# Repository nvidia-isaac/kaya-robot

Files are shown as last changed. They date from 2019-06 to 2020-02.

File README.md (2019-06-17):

# kaya-robot

Kaya is an open-source robot powered by NVIDIA's Isaac SDK and the Jetson Nano. 

This repository contains 3D-printable and editable CAD files in the `cad-files` folder (STL, STEP, IGES), as well as a complete bill of materials and assembly instructions for [NVIDIA Kaya](doc/assemble_kaya.md) in the `doc` folder.

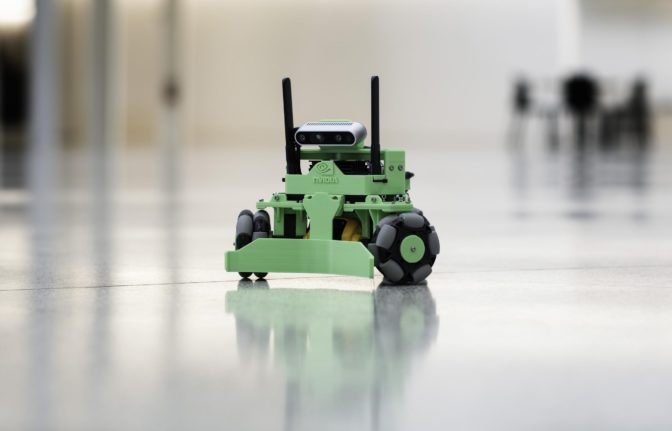
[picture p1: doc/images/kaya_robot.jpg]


Kaya is intended to provide an accessible starting point for robotics development, and a number of sample apps for Kaya come packaged with the Isaac SDK.

For more information on Kaya and the Isaac SDK, see the [NVIDIA Isaac SDK Documentation](https://docs.nvidia.com/isaac/isaac/doc/index.html).

You can also join NVIDIA's developer community to ask questions and share your projects on the [Isaac SDK Forums](https://devtalk.nvidia.com/default/board/375/sdk/)!

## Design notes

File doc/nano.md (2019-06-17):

How to Get Started With Jetson Nano
===================================

This section describes how to flash, install wireless connectivity, and
run Isaac SDK sample applications on the Jetson Nano device. To get
started with Nano in general, from the very beginning, see [Getting
Started with Jetson Nano Developer
Kit](https://developer.nvidia.com/embedded/learn/get-started-jetson-nano-devkit).

How to Flash Jetson Nano
------------------------

Nano can be flashed in two ways:

-   Via an SD Card: See the procedures in [Getting Started with Jetson
    Nano Developer
    Kit](https://developer.nvidia.com/embedded/learn/get-started-jetson-nano-devkit).
-   Via SDK Manager: See the procedures in [SDK Manager User
    Guide](https://docs.nvidia.com/sdk-manager)

Use those documents to determine the best method for your use case.

Connecting a Wi-Fi/Bluetooth Card
---------------------------------

The Intel 8265 is used for Wi-Fi and Bluetooth connectivity. Use the
following steps to install a Wi-Fi/Bluetooth card for Jetson Nano.

1.  To access the M.2 slot on the carrier board, remove the two screws
    on the side and open the SODIMM latches using both your hands.

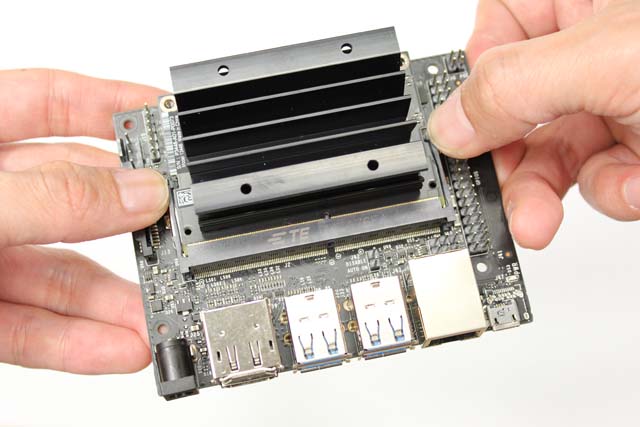
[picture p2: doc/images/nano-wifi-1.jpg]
    

2.  When the Jetson Nano module pops up, slide it out gently.

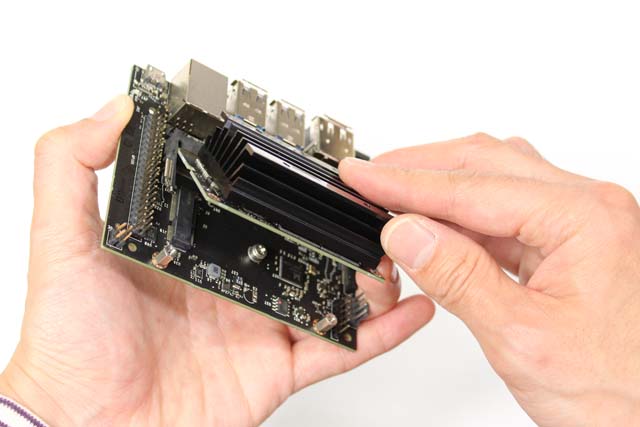
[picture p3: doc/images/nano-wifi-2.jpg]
    

3.  Take out the Intel wireless card, attach antenna on its U.FL sockets
    before inserting the card to the M.2 socket. Attaching the antena on
    the sockets requires a patience and getting used to. Use your nail
    to gently apply a force. You don't need that much force to clamp
    that in once you are in the right position.

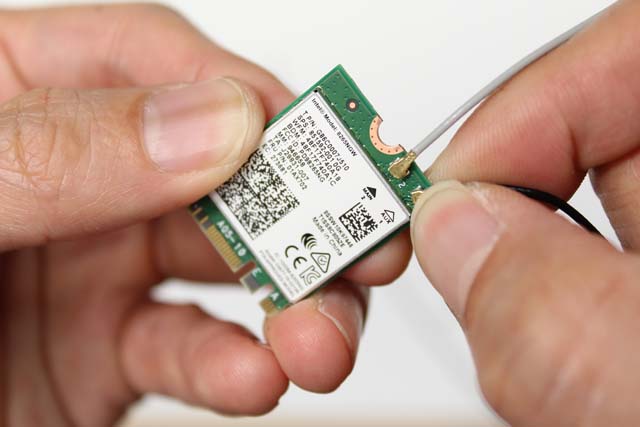
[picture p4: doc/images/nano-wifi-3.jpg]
    

4.  Slide the Intel 8265 card into the socket.

    

5.  Fix the Intel 8265 card in place with a screw, and replace the
    Jeston Nano module. Make sure to use the correct screws in each
    case.

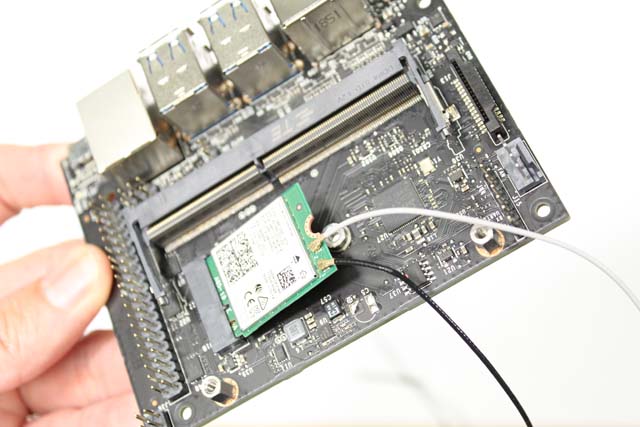
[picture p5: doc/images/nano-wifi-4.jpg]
    

Getting the IP Address
----------------------

Obtain the IP address of Jetson Nano with the following steps:

1.  If necessary, connect a keyboard, mouse, and display, and boot the
    device as shown in the [Setup and First
    Boot](https://developer.nvidia.com/embedded/learn/get-started-jetson-nano-devkit#setup)
    section of Getting Started with Jetson Nano Developer Kit.
2.  At a terminal prompt, enter the following command:

        bob@jetson:~/$ ip addr show

Sample Applications to Run on Jetson Nano
-----------------------------------------

This section describes the steps to run two sample applications on
Jetson Nano. The first does not require any peripherals. The second one
is a more useful application that requires a camera to be connected.

Other applications can be also deployed and run using the methods
described here.

### Ping

1.  On the host system where the Isaac SDK is installed, start by typing
    the following on your host machine with Isaac SDK.

>     bob@desktop:~/isaac$ /engine/build/deploy.sh -d jetpack42 -h <nano_ip> -p //apps/tutorials/ping:ping-pkg
>
> You might need to use the --remote\_user USER flag if the user name on
> the robot is not nvidia.

1.  Change to the directory on your Jetson Nano and run the application
    with the following commands:

>     bob@jetson:~/$ cd deploy/bob/ping-pkg/
>     bob@jetson:~/deploy/bob/ping-pkg$ ./apps/tutorials/ping/ping

Where "bob" is your username on the host system. You should see "Hello
World!" being printed every 1.5 seconds.

### OpenCV Edge Detection

1.  For this sample, connect a camera to one of the USB ports on the
    Jetson Nano.
2.  On the host system where the Isaac SDK is installed, type the
    following command:

>     bob@jetson:~/isaac$ ./engine/build/deploy.sh -d jetpack42 -h <nano_ip> -p //apps/tutorials/opencv_edge_detection:opencv_edge_detection-pkg
>
> You might need to use the --remote\_user USER flag if the user name on
> the robot is not nvidia.

1.  Change to the directory on your Jetson Nano and run the application
    with the following commands:

>     bob@jetson:~/$ cd deploy/bob/opencv_edge_detection-pkg/
>     bob@jetson:~/deploy/bob/opencv_edge_detection-pkg/$ ./apps/tutorials/opencv_edge_detection/opencv_edge_detection

1.  To view the results, load http://&lt;nano\_ip&gt;:3000/ in your
    browser. Make sure that the application is running when you are
    loading the webpage.

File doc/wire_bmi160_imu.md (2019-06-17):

Wire the BMI160 IMU to the Jetson Nano or Xavier
================================================

The Bosch Sensortec BMI160 Inertial Measurement Unit attaches to the
Jetson board via the 40 pin GPIO Expansion Header. The IMU sample app is
configured to look for the BMI160 on I2C bus 1. Here are instructions on
how to wire the IMU to I2C bus 1.

Jetson Nano
-----------

From the BMI160 to the Jetson Nano 40 pin connector attach VIN to GPIO
1, GND to GPIO 6, SCL to GPIO 5, and SDA to GPIO 3.

<table style="width:25%;">
<colgroup>
<col width="12%" />
<col width="12%" />
</colgroup>
<thead>
<tr class="header">
<th>BMI160</th>
<th>GPIO</th>
</tr>
</thead>
<tbody>
<tr class="odd">
<td>VIN</td>
<td><blockquote>
<p>1</p>
</blockquote></td>
</tr>
<tr class="even">
<td>GND</td>
<td><blockquote>
<p>6</p>
</blockquote></td>
</tr>
<tr class="odd">
<td>SCL</td>
<td><blockquote>
<p>5</p>
</blockquote></td>
</tr>
<tr class="even">
<td>SDA</td>
<td><blockquote>
<p>3</p>
</blockquote></td>
</tr>
</tbody>
</table>

It is a little hard to see the wiring in these photos since the Nano is
attached to a robot, so multiple photos are included.

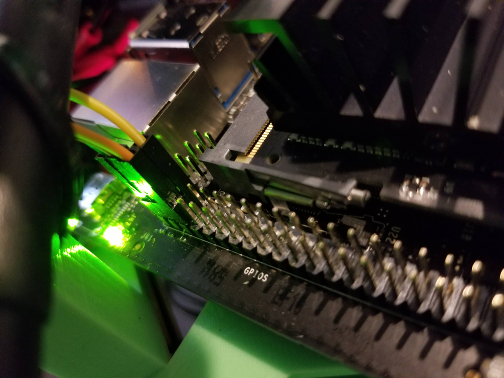
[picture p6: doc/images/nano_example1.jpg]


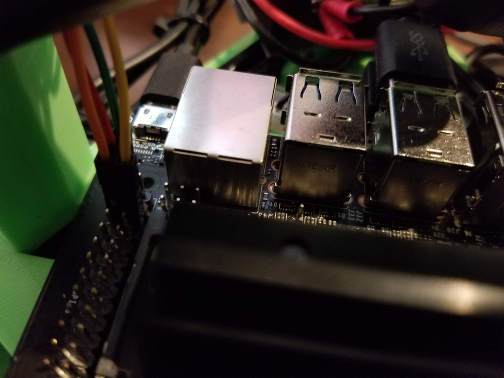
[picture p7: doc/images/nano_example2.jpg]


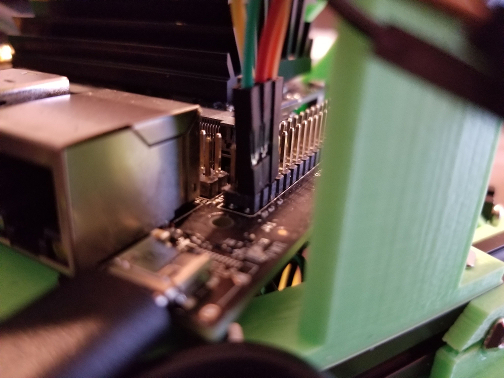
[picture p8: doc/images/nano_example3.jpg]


Wiring:

    Green wire:  VIN => GPIO 1
    Red wire:    SDA => GPIO 3
    Orange wire: SCL => GPIO 5
    Yellow wire: GND => GPIO 6

Jetson Xavier
-------------

From the BMI160 to the Jetson Xavier 40 pin connector attach VIN to GPIO
17, GND to GPIO 25, SCL to GPIO 28, and SDA to GPIO 27.

<table style="width:25%;">
<colgroup>
<col width="12%" />
<col width="12%" />
</colgroup>
<thead>
<tr class="header">
<th>BMI160</th>
<th>GPIO</th>
</tr>
</thead>
<tbody>
<tr class="odd">
<td>VIN</td>
<td><blockquote>
<p>17</p>
</blockquote></td>
</tr>
<tr class="even">
<td>GND</td>
<td><blockquote>
<p>25</p>
</blockquote></td>
</tr>
<tr class="odd">
<td>SCL</td>
<td><blockquote>
<p>28</p>
</blockquote></td>
</tr>
<tr class="even">
<td>SDA</td>
<td><blockquote>
<p>27</p>
</blockquote></td>
</tr>
</tbody>
</table>

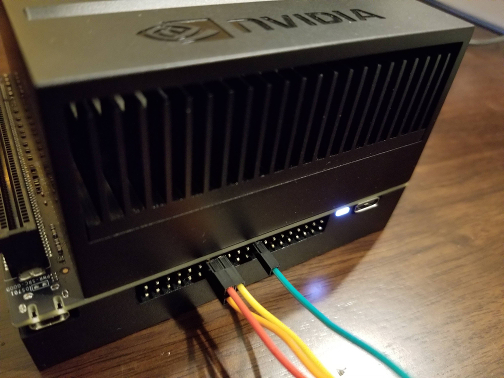
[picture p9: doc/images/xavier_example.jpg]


Wiring:

    Green wire:  VIN => GPIO 17
    Yellow wire: GND => GPIO 25
    Red wire:    SDA => GPIO 27
    Orange wire: SCL => GPIO 28

User Permissions
----------------

On the Jetson, `/dev/i2c-*` is owned by the user `root`, and are in the
group `i2c`. The sample app will need to run as either root, or by a
user in the i2c group.

To add the current user to the i2c group, use the following command:

    sudo usermod -a -G i2c $USER

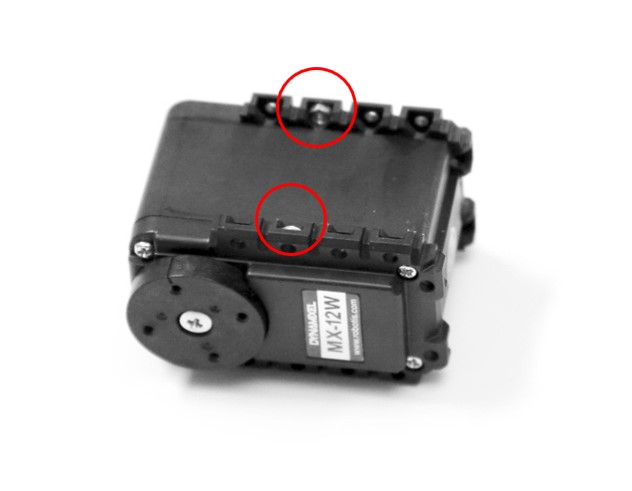
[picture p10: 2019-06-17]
doc/images/kaya2.jpg

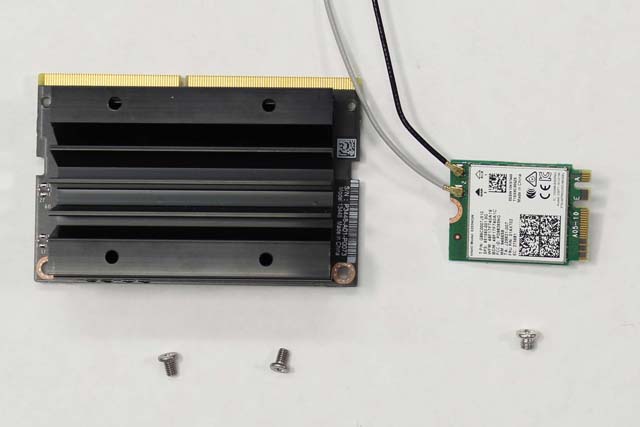
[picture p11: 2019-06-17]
doc/images/nano-wifi-5.jpg

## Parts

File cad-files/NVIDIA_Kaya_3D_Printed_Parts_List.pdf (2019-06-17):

# NVIDIA Kaya 3D Printed Parts List

All parts are shown in their intended print orientation (ie. print bed downward). Kaya_Nano_Base ● 0.15mm layer height suggested ● No support

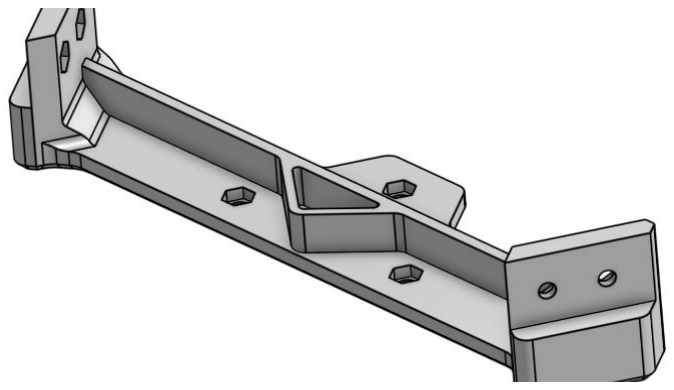
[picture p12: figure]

Kaya_Realsense_Bridge ● 0.15mm layer height suggested ● No support

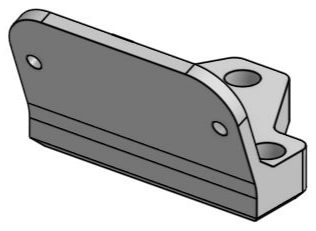
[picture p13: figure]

Kaya_Realsense_Mount ● 0.15mm layer height suggested ● No support

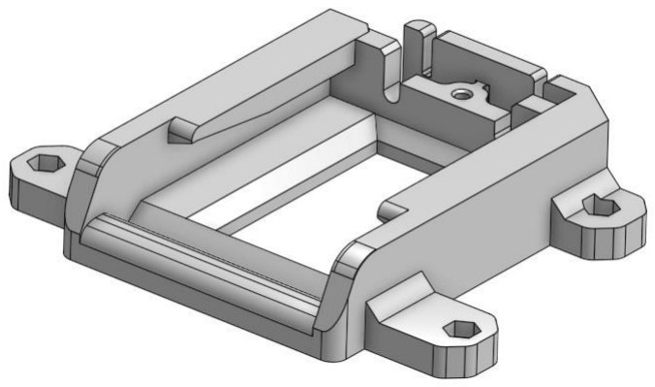
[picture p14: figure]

Kaya_Battery_Holder ● 0.15mm layer height suggested ● Support for internal undercut rails

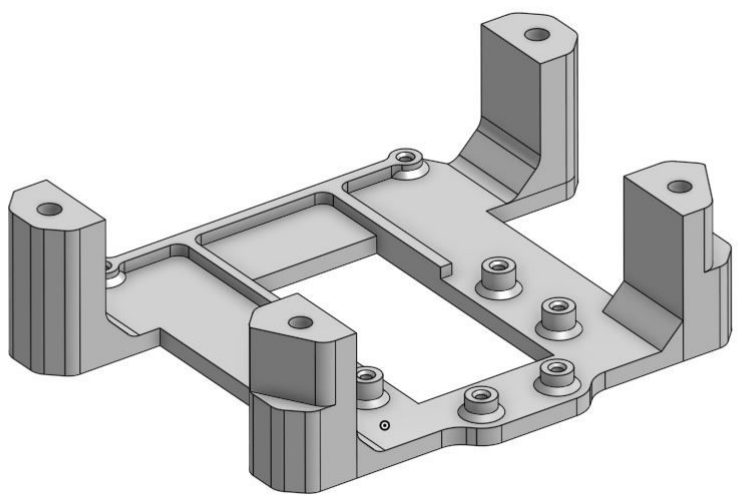
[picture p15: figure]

Kaya_Electronics_Bay ● 0.15mm layer height suggested ● No support

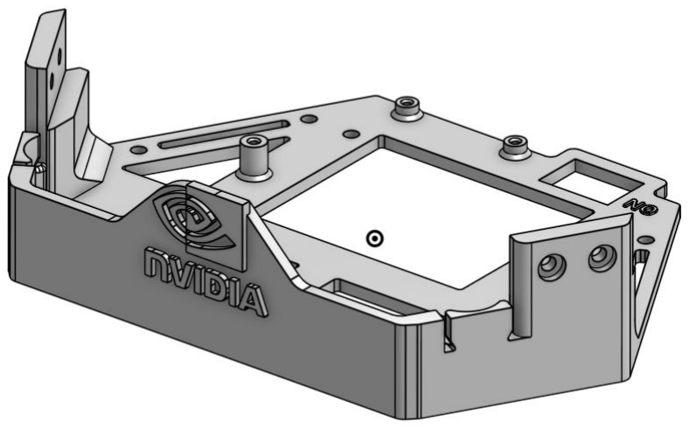
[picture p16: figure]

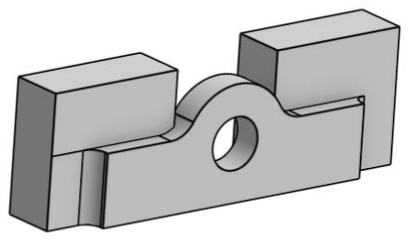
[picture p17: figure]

Kaya_Battery_Terminal_Holder ● 0.15mm layer height suggested ● No support

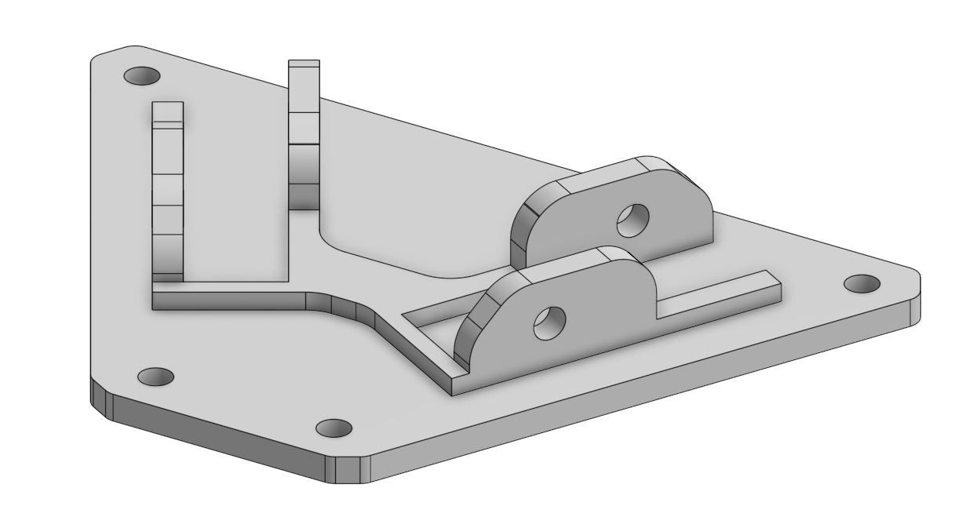
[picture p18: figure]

Kaya_Motor_Top_Plate ● 0.15mm layer height suggested ● No support *3x parts per unit

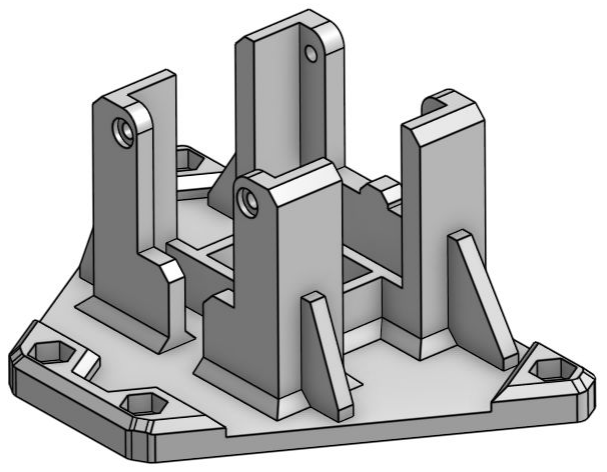
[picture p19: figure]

Kaya_Motor_Bottom_Plate ● 0.15mm layer height suggested ● No support *3x parts per unit


Kaya_Wheel_Hub_Outside ● 0.15mm layer height suggested ● No support *3x parts per unit

Kaya_Wheel_Hub_Inside ● 0.15mm layer height suggested ● No support *3x parts per unit


Kaya_Pusher_Mount ● 0.15mm layer height suggested ● No support


Kaya_Pusher ● 0.15mm layer height suggested ● Support for rear


Kaya_Terminal_Block_Cover ● 0.15mm layer height suggested ● Support for overhang mount hole

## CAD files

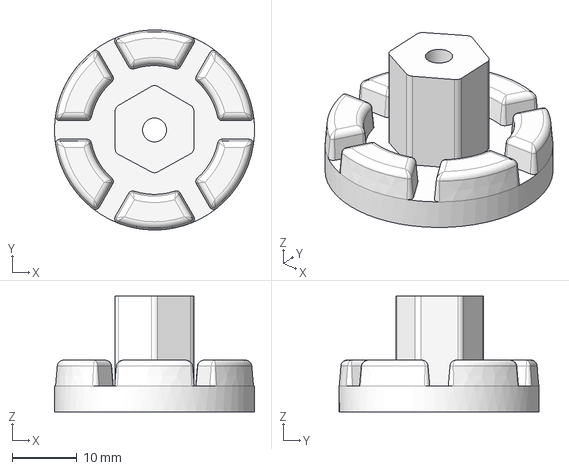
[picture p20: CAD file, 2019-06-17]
cad-files/Kaya_Wheel_Hub_Outside.step
30.9 x 30.9 x 17.9 mm

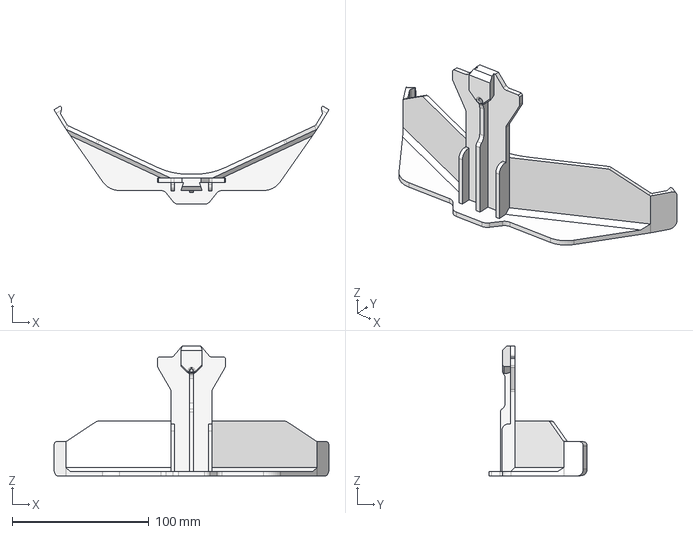
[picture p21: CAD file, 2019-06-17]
cad-files/Kaya_Pusher.step
201.5 x 72.0 x 95.0 mm

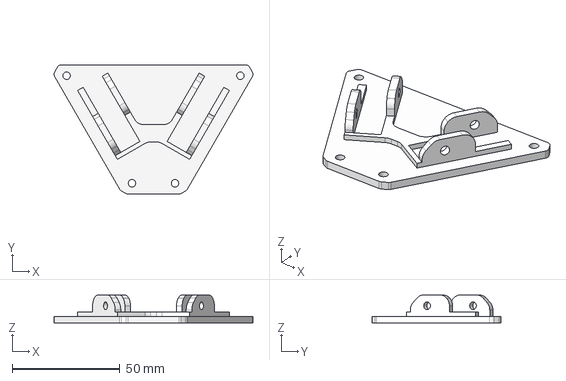
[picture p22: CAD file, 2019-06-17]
cad-files/Kaya_Motor_Top_Plate.step
92.5 x 60.0 x 13.0 mm

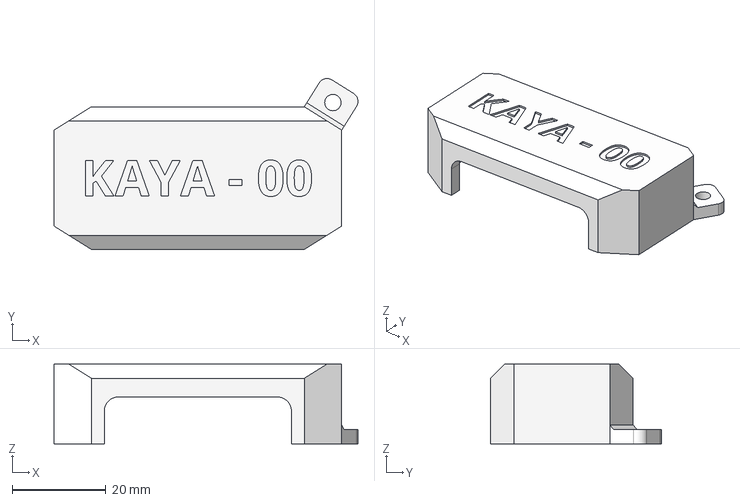
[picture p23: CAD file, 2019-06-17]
cad-files/Kaya_Terminal_Block_Cover.step
65.0 x 36.5 x 17.0 mm

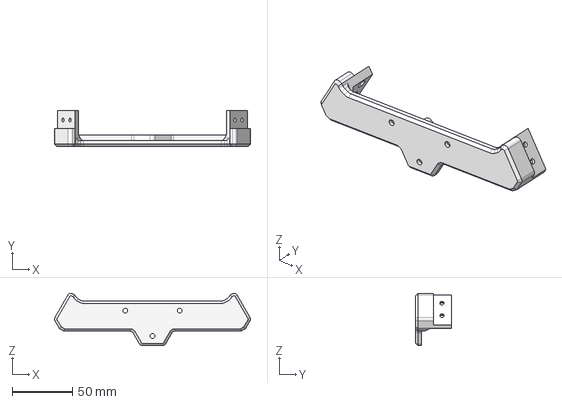
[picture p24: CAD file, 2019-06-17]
cad-files/Kaya_Realsense_Bridge.step
162.2 x 30.0 x 43.4 mm

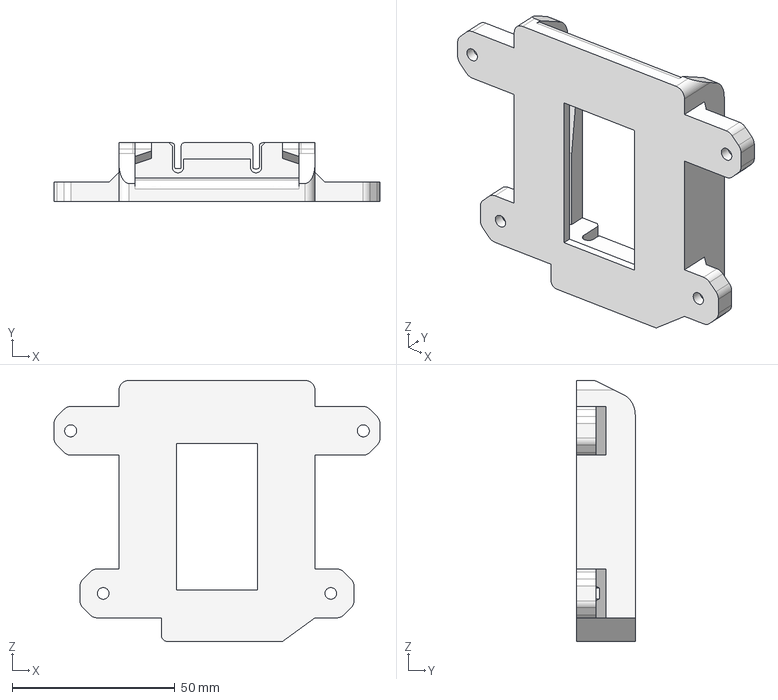
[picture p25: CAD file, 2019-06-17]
cad-files/Kaya_Battery_Holder.step
100.3 x 18.0 x 80.3 mm

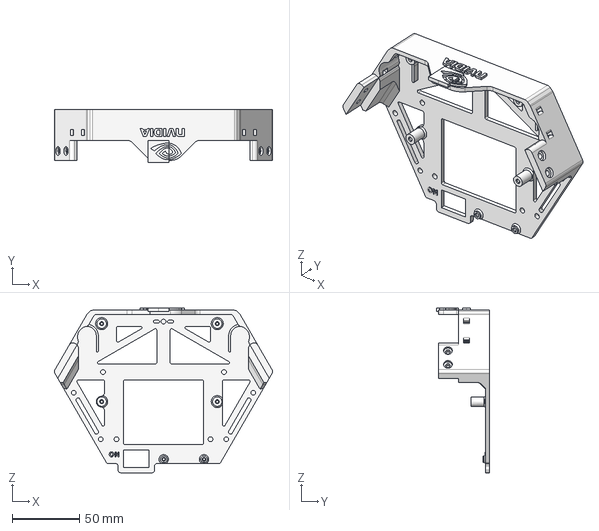
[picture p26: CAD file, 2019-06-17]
cad-files/Kaya_Nano_Base.step
162.2 x 39.6 x 122.4 mm

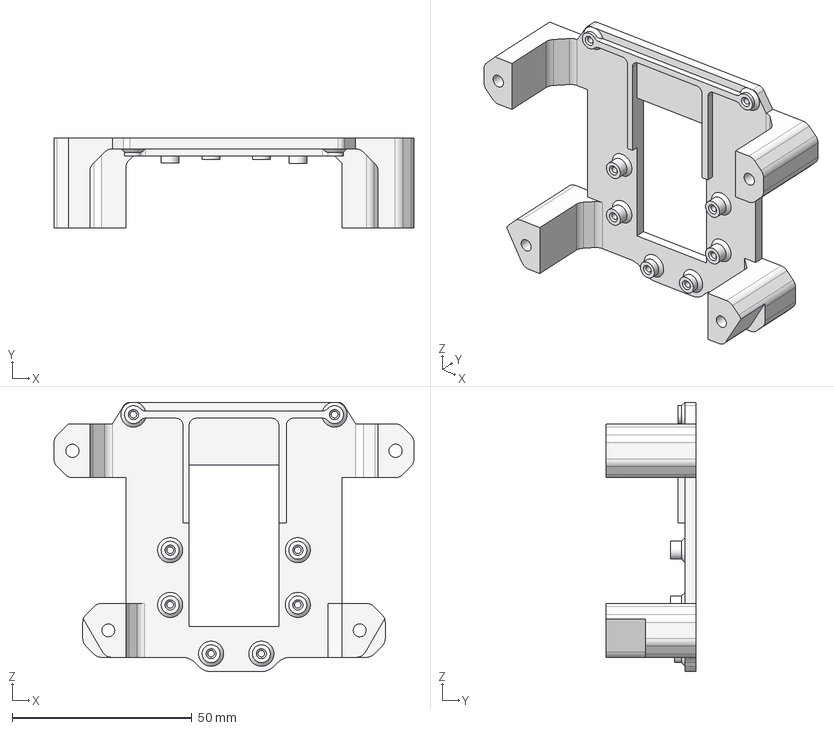
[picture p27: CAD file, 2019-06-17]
cad-files/Kaya_Electronics_Bay.step
100.3 x 25.0 x 75.0 mm

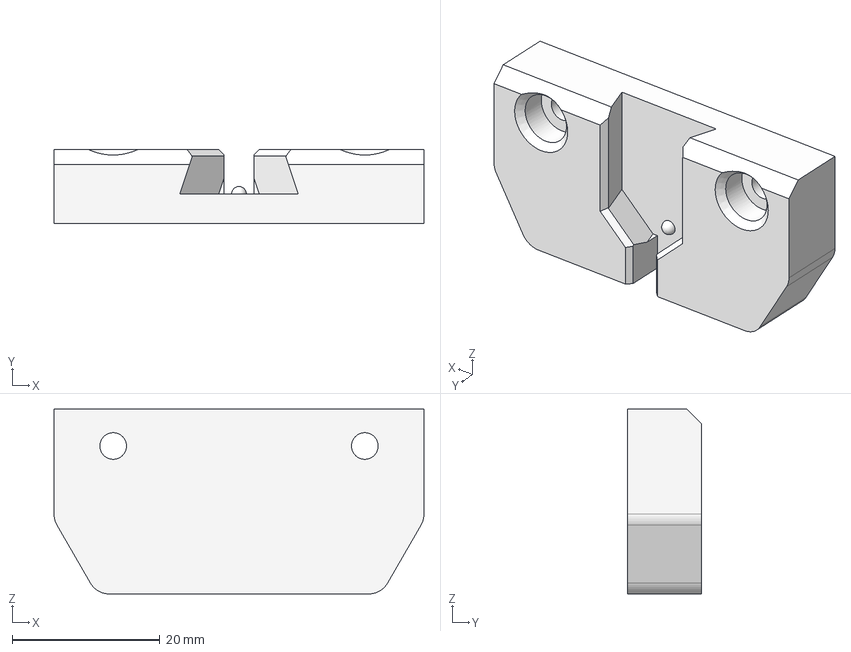
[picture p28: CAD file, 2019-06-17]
cad-files/Kaya_Pusher_Mount.step
50.0 x 10.0 x 25.0 mm

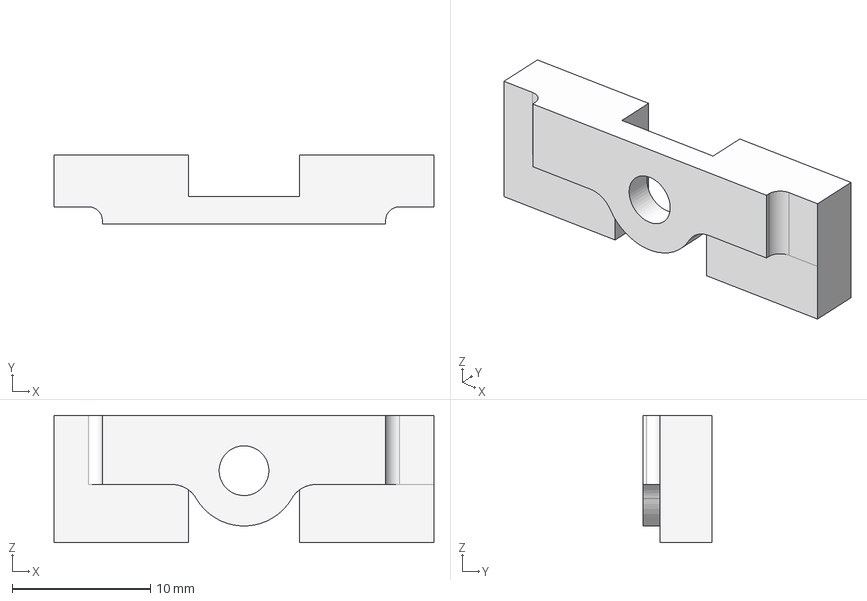
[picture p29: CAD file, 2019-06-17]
cad-files/Kaya_Battery_Terminal_Holder.step
27.5 x 5.00 x 9.20 mm

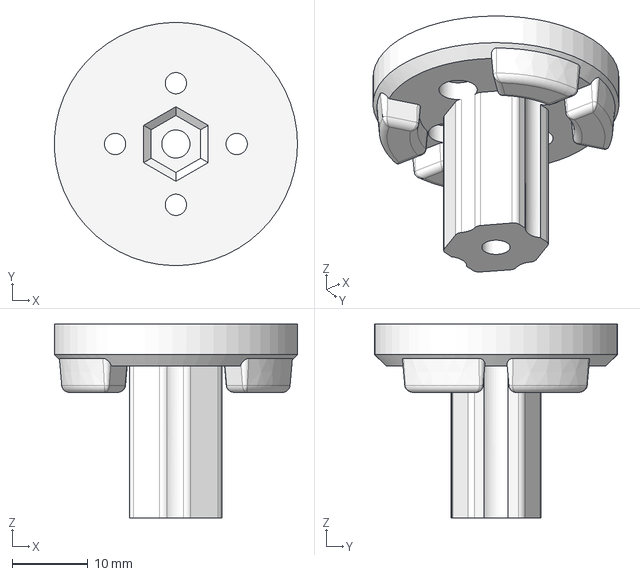
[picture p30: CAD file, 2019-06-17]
cad-files/Kaya_Wheel_Hub_Inside.step
32.0 x 32.0 x 25.5 mm

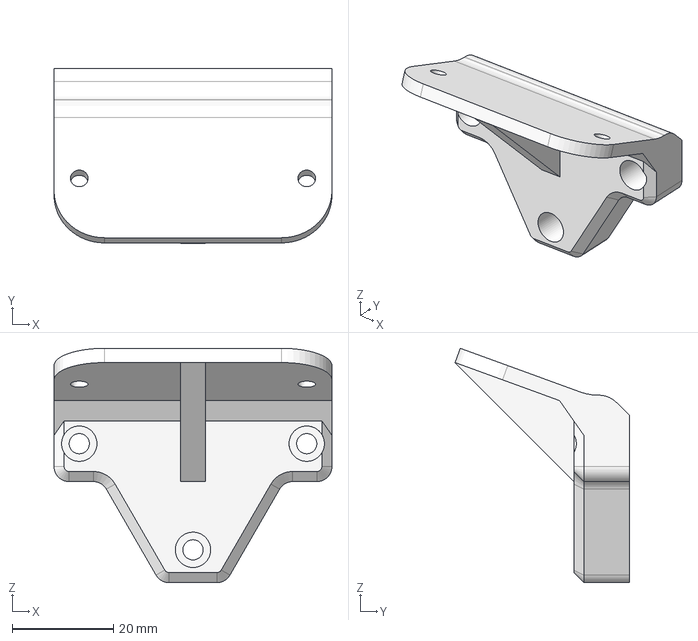
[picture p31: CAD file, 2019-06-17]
cad-files/Kaya_Realsense_Mount.step
55.0 x 34.6 x 46.4 mm

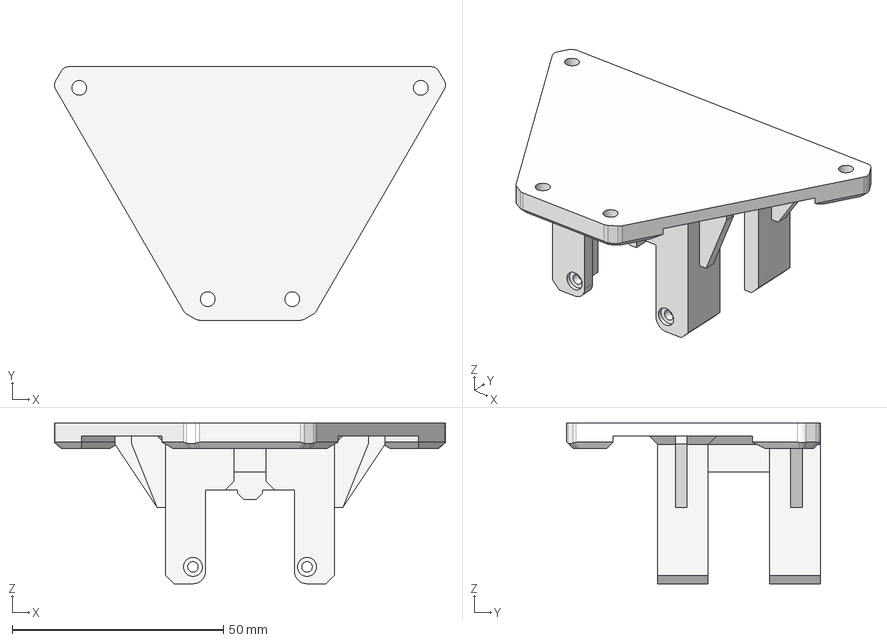
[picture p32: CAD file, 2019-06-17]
cad-files/Kaya_Motor_Bottom_Plate.step
92.5 x 60.0 x 38.0 mm

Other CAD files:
cad-files/Kaya_Battery_Holder.iges
cad-files/Kaya_Battery_Holder.stl
cad-files/Kaya_Battery_Terminal_Holder.iges
cad-files/Kaya_Battery_Terminal_Holder.stl
cad-files/Kaya_Electronics_Bay.iges
cad-files/Kaya_Electronics_Bay.stl
cad-files/Kaya_Motor_Bottom_Plate.iges
cad-files/Kaya_Motor_Bottom_Plate.stl
cad-files/Kaya_Motor_Top_Plate.iges
cad-files/Kaya_Motor_Top_Plate.stl
cad-files/Kaya_Nano_Base.iges
cad-files/Kaya_Nano_Base.stl
cad-files/Kaya_Pusher.iges
cad-files/Kaya_Pusher.stl
cad-files/Kaya_Pusher_Mount.iges
cad-files/Kaya_Pusher_Mount.stl
cad-files/Kaya_Realsense_Bridge.iges
cad-files/Kaya_Realsense_Bridge.stl
cad-files/Kaya_Realsense_Mount.iges
cad-files/Kaya_Realsense_Mount.stl
cad-files/Kaya_Terminal_Block_Cover.iges
cad-files/Kaya_Terminal_Block_Cover.stl
cad-files/Kaya_Wheel_Hub_Inside.iges
cad-files/Kaya_Wheel_Hub_Inside.stl
cad-files/Kaya_Wheel_Hub_Outside.iges

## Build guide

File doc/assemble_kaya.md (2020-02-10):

NVIDIA Kaya
===========

Kaya is a robot developed as a platform to demonstrate the power and
flexibility of the Isaac Robot Engine running on the NVIDIA Jetson Nano
platform. It has been intentionally designed using 3D printed parts and
hobbyist components to be as accessible as possible.



The Kaya Robot

Kaya features a three-wheeled holonomic drive which allows it to move in
any direction, regardless of where it is facing. A RealSense depth
camera allows Kaya to see the world around it in 3D, enabling features
like mapping, localization, and object recognition. An on-board IMU and
position feedback from the wheel motors provide accurate odometry
information. Power is provided via an easily-swapped and fast-charging
power tool battery. Outfitting the Jetson Nano with a Wi-Fi/Bluetooth
card allows you to interact with the robot using Isaac Sight over Wi-Fi,
and also allows you to connect a gamepad controller via Bluetooth.

Use the instructions in this section to build and operate your own Kaya
robot.

Parts
-----

For a list of 3D printed parts, and STL/STEP/IGES files for creating the parts,
see either the [`cad-files`](https://github.com/nvidia-isaac/kaya-robot/tree/master/cad-files) folder in this GitHub repository, or the [Isaac Developer
Downloads](https://developer.nvidia.com/isaac/downloads) website.

The following is a list of the off-the-shelf components needed for
building Kaya. Prices shown are approximate and subject to change by
vendors. Many of these components or suitable replacements are available
from a wide variety of sources, which you are encouraged to explore.

<table>
<thead>
<tr class="header">
<th><strong>PART NAME</strong></th>
<th><strong>VENDOR PART #</strong></th>
<th><strong>SOURCE</strong></th>
<th><strong>QTY</strong></th>
<th><strong>APPROX COST</strong></th>
</tr>
</thead>
<tbody>
<tr class="odd">
<td>3D Printed Parts</td>
<td>-</td>
<td><em>See 3D Printed Parts List</em></td>
<td>-</td>
<td>-</td>
</tr>
<tr class="even">
<td>NVIDIA Jetson Nano Developer Kit</td>
<td>945-13450-0000-000</td>
<td><a href="https://developer.nvidia.com/buy-jetson?product=jetson_nano">NVIDIA</a></td>
<td>1</td>
<td>$99.00</td>
</tr>
<tr class="odd">
<td>MicroSD Card (32GB)</td>
<td>SDSQUNC-032G-GN6MA</td>
<td><a href="https://www.amazon.com/SanDisk-microSDHC-Standard-Packaging-SDSQUNC-032G-GN6MA/dp/B010Q57T02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">Amazon - SanDisk</a></td>
<td>1</td>
<td>$8.00</td>
</tr>
<tr class="even">
<td>Intel Dual Band Wireless-Ac 8265 W/Bt</td>
<td>8265NGW</td>
<td><a href="https://www.amazon.com/Intel-Dual-Band-Wireless-Ac-8265/dp/B01MZA1AB2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">Amazon - Intel</a></td>
<td>1</td>
<td>$25.00</td>
</tr>
<tr class="odd">
<td>Dual Band Wi-Fi Antennas &amp; IPEX4 to RP-SMA Cables</td>
<td>CHAOHANG 6484109</td>
<td><a href="https://www.amazon.com/CHAOHANG-RP-SMA-Antenna-Soldering-Wireless/dp/B01E29566W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">Amazon</a></td>
<td>1</td>
<td>$13.00</td>
</tr>
<tr class="even">
<td>Intel RealSense Depth Camera D435</td>
<td>961448</td>
<td><a href="https://click.intel.com/intelr-realsensetm-depth-camera-d435.html">Intel</a></td>
<td>1</td>
<td>$179.00</td>
</tr>
<tr class="odd">
<td>Bosch GY-BMI160 6DOF IMU Board (Generic Breakout)</td>
<td>GY-BMI160</td>
<td><a href="https://www.amazon.com/s?k=GY-BMI160">Amazon / eBay / AliExpress</a></td>
<td>1</td>
<td>$5.00</td>
</tr>
<tr class="even">
<td>Dynamixel MX-12W Servo Motor</td>
<td>902-0086-000</td>
<td><a href="http://www.robotis.us/dynamixel-mx-12w/">Robotis</a></td>
<td>3</td>
<td>$197.70</td>
</tr>
<tr class="odd">
<td>USB2AX v3.2a or U2D2</td>
<td>XE-USB2AX (for USB2AX v3.2a) or RO-902-0132-000 (for U2D2)</td>
<td><a href="https://www.trossenrobotics.com/usb2ax">Trossen Robotics USB2AX v3.2a</a> or <a href="https://www.trossenrobotics.com/dynamixel-u2d2.aspx">Trossen Robotics U2D2</a></td>
<td>1</td>
<td>$39.95 (for USB2AX v3.2a) or $49.90 (for U2D2)</td>
</tr>
<tr class="even">
<td>Dynamixel 6 Port AX/MX Power Hub</td>
<td>IL-3PHUB</td>
<td><a href="https://www.trossenrobotics.com/6-port-ax-mx-power-hub">Trossen Robotics</a></td>
<td>1</td>
<td>$7.95</td>
</tr>
<tr class="odd">
<td>VEX 3.25&quot; Omni-Directional Wheel</td>
<td>217-4775</td>
<td><a href="https://www.vexrobotics.com/omni-wheels.html">VEX Robotics</a></td>
<td>3</td>
<td>$53.97</td>
</tr>
<tr class="even">
<td>DeWALT 20V MAX 2AH Li-ion Battery</td>
<td>DCB203</td>
<td><a href="https://www.amazon.com/DEWALT-DCB203-Compact-Li-Ion-Battery/dp/B00BYKVMES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">Amazon - DeWALT</a></td>
<td>1</td>
<td>$45.00</td>
</tr>
<tr class="odd">
<td>DeWALT 20V MAX Li-ion Battery Charger</td>
<td>DCB107</td>
<td><a href="https://www.amazon.com/dp/B06X94PH92/ref=psdc_8106529011_t1_B00X6BWHA6">Amazon - DeWALT</a></td>
<td>1</td>
<td>$34.75</td>
</tr>
<tr class="even">
<td>5V 6A DC-DC Step-Down Regulator</td>
<td>D24V60F5</td>
<td><a href="https://www.pololu.com/product/2865">Pololu</a></td>
<td>1</td>
<td>$19.95</td>
</tr>
<tr class="odd">
<td>12V 5A DC-DC Step-Down Regulator</td>
<td>EA60-12V</td>
<td><a href="https://www.amazon.com/gp/product/B01LY4RANA/ref=ppx_yo_dt_b_asin_title_o00_s00?ie=UTF8&amp;psc=1">Amazon</a></td>
<td>1</td>
<td>$9.50</td>
</tr>
<tr class="even">
<td>2.1 x 5.5mm Male Barrel Plug Pigtail</td>
<td>B072BXB2Y8</td>
<td><a href="https://www.amazon.com/gp/product/B072BXB2Y8/ref=ppx_yo_dt_b_asin_title_o00_s00?ie=UTF8&amp;psc=1">Amazon</a></td>
<td>1</td>
<td>$0.94</td>
</tr>
<tr class="odd">
<td>Rocker Switch</td>
<td>7395K28</td>
<td><a href="https://www.mcmaster.com/7395k28">McMaster-Carr</a></td>
<td>1</td>
<td>$6.76</td>
</tr>
<tr class="even">
<td>Terminal Block</td>
<td>7527K44</td>
<td><a href="https://www.mcmaster.com/7527k44">McMaster-Carr</a></td>
<td>1</td>
<td>$2.24</td>
</tr>
<tr class="odd">
<td>Terminal Block Jumpers</td>
<td>7527K59</td>
<td><a href="https://www.mcmaster.com/7527k59">McMaster-Carr</a></td>
<td>2</td>
<td>$0.49</td>
</tr>
<tr class="even">
<td>Wire End/Terminal Kit</td>
<td>HC28-6</td>
<td><a href="https://www.amazon.com/Accessbuy-Insulated-Electrical-Connector-Connectors/dp/B01L3MSLO0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">Amazon</a></td>
<td>-</td>
<td>$10.00</td>
</tr>
<tr class="odd">
<td>18AWG Electrical Wire (Red and Black)</td>
<td>-</td>
<td><a href="https://www.amazon.com/Electrical-Gauge-Silicone-Cable-Black/dp/B0746HMTPP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">Amazon</a></td>
<td>-</td>
<td>$5.00</td>
</tr>
<tr class="even">
<td>Female-Female Electrical Jumper Wires</td>
<td>-</td>
<td><a href="https://www.amazon.com/GenBasic-Solderless-Dupont-Compatible-Breadboard-Prototyping/dp/B077NH83CJ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">Amazon</a></td>
<td>4</td>
<td>$5.00</td>
</tr>
<tr class="odd">
<td>MakerBeam 150x10x10mm Beams</td>
<td>bamb150p06</td>
<td><a href="https://www.amazon.com/MakerBeam-150x10x10mm-beam-black-anodised/dp/B00G2DNT4I">Amazon - MakerBeam</a></td>
<td>3</td>
<td>$5.00</td>
</tr>
<tr class="even">
<td>MakerBeam 25 pieces T-slot nuts inc screws</td>
<td>101619</td>
<td><a href="https://www.amazon.com/gp/product/B016OJNLJ2/ref=oh_aui_detailpage_o01_s01?ie=UTF8&amp;psc=1">Amazon - MakerBeam</a></td>
<td>-</td>
<td>$17.00</td>
</tr>
<tr class="odd">
<td>M3 18mm threaded standoff</td>
<td>95947A525</td>
<td><a href="https://www.mcmaster.com/95947a525">McMaster-Carr</a></td>
<td>3</td>
<td>$3.66</td>
</tr>
<tr class="even">
<td>M3 x 35mm Socket Head Screw</td>
<td>91292A033</td>
<td><a href="https://www.mcmaster.com/91292a033">McMaster-Carr</a></td>
<td>3</td>
<td>$3.54</td>
</tr>
<tr class="odd">
<td>M3 x 8mm Socket Head Screw</td>
<td>91292A112</td>
<td><a href="https://www.mcmaster.com/91292a112">McMaster-Carr</a></td>
<td>-</td>
<td>$4.29</td>
</tr>
<tr class="even">
<td>M3 x 5mm Socket Head Screw</td>
<td>91292A110</td>
<td><a href="https://www.mcmaster.com/91292a110">McMaster-Carr</a></td>
<td>-</td>
<td>$4.72</td>
</tr>
<tr class="odd">
<td>M3 Hex Nuts</td>
<td>90591A250</td>
<td><a href="https://www.mcmaster.com/90591a250">McMaster-Carr</a></td>
<td>-</td>
<td>$2.21</td>
</tr>
<tr class="even">
<td>M2 x 6mm Phillips Screw</td>
<td>92010A003</td>
<td><a href="https://www.mcmaster.com/92010a003">McMaster-Carr</a></td>
<td>-</td>
<td>$4.39</td>
</tr>
<tr class="odd">
<td>
</td>
<td></td>
<td></td>
<td></td>
<td><strong>$812.87</strong></td>
</tr>
</tbody>
</table>

Dynamixel U2D2 & USB2AX Interchangeability
------------------------------------------

To communicate with the Dynamixel servo motors, either the USB2AX or
U2D2 serial converters may be used. (The U2D2 converter is available as
[Trossen Robotics
RO-902-1032-000](https://www.trossenrobotics.com/dynamixel-u2d2.aspx)
for $49.90. Price is approximate and subject to change by the vendor.)

You must specify the USB device name of the converter in the `usb_port`
parameter of the isaac.KayaBaseDriver component API so that your
application can communicate with it. For the Kaya sample applications
included in Isaac SDK, this is found in
`\apps\kaya\robots\kaya_v<version>.config.json`. In the following
example, the U2D2 serial converter is specified.

    {
       "kaya_driver": {
          "isaac.KayaBaseDriver": {
             "usb_port": "/dev/ttyUSB0"
          }
       }
    }

The devices have the following USB device names.

-   USB2AX: ttyACM0
-   U2D2: ttyUSB0

See the Component API section of this documentation describing
isaac.KayaBaseDriver for more information.

Wiring Diagram
--------------

See below for a wiring diagram for the Kaya robot. You may find it
useful to reference this during the assembly process. Click for a larger
version.

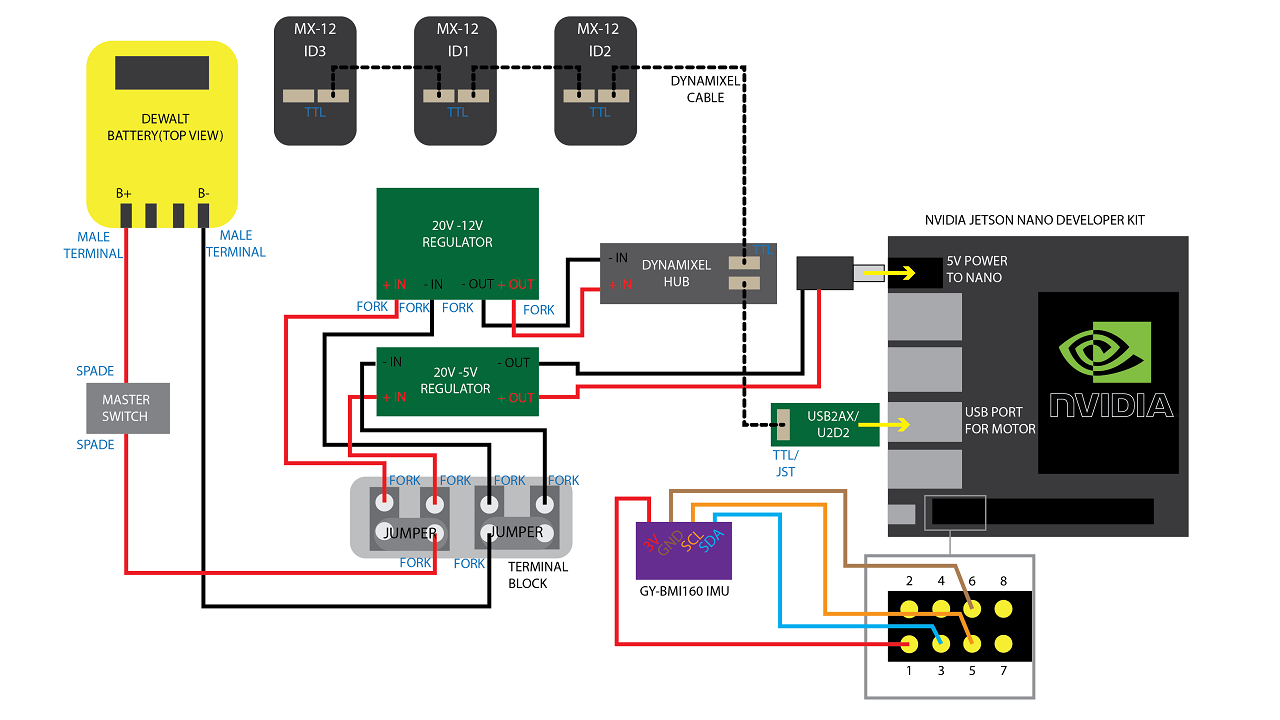
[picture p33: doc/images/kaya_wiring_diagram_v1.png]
Wiring Diagram for the NVIDIA Kaya Robot


Wiring Diagram for the Kaya Robot

Assembly Instructions
---------------------

This section describes step-by-step assembly of the Kaya robot.

The underscore-delimited names that appear in parentheses in the steps
below are the names of the 3D-printed parts. See "Parts" section for links
to that list.

**1 Assign IDs to the Dynamixel Motors**

When first purchased, the Dynamixel motors are all be assigned ID “1,”
and must be assigned unique IDs and properly configured before being
connected together on Kaya. This procedure requires a USB serial adapter
(USB2AX or U2D2), an external 12V power source (the 12V DC-DC converter
on Kaya), and a PC which on which to run the RoboPlus v1 software.

RoboPlus v2 does not work with MX-12W. See
[<http://www.robotis.us/roboplus1/>](http://www.robotis.us/roboplus1/)
to download the RoboPlus v1 application.

You can also complete this step after the rest of Kaya is assembled.
Just be aware that you should only connect one motor at a time to avoid
duplicate IDs.

To assign IDs to the motors:

1.  Start the RoboPlus v1 application.
2.  Connect the USB serial converter to the desktop.
3.  Connect each Dynamixel motor to the serial adapter.
4.  Connect the Dynamixel motor to external (12V) power.
5.  Launch Dynamixel Wizard in the RoboPlus v1 application.
6.  Open Port (top menu) to detect connected motors.
7.  Click on the correct motor, assign the ID \# below and wheel mode.
    Click Apply.

    > -   Left: ID 1
    > -   Rear: ID 2
    > -   Right: ID 3

8.  Repeat step 7 for each motor, and annotate the ID placard for each
    motor accordingly.

**2 Install Dynamixel Servo Motors (3 per Robot)**

1.  Insert 4 M2 nuts from the Dynamixel MX-12W motor kits into the
    second slot up from the horn (servo head) on all sides. Press firmly
    to secure.
2.  Install each motor into a motor bottom plate
    (Kaya\_Motor\_Bottom\_Plate) using 4 M2 screws from the Dynamixel
    MX-12W motor kits.

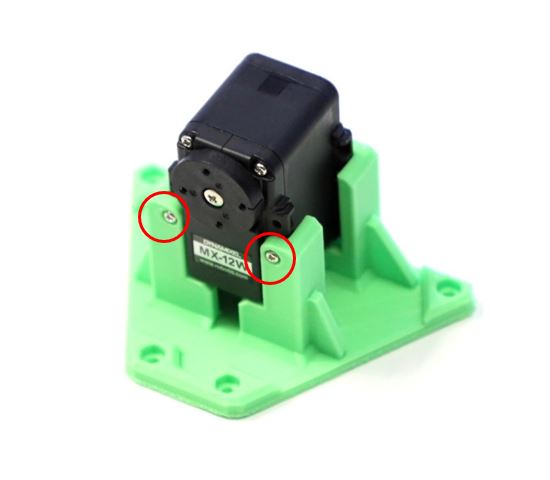
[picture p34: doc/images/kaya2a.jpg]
    

**3 Assemble the Inside Wheel Hub (3 per Robot)**

1.  Insert an 18mm M3 standoff into hex hole on the back side of the hub
    (Kaya\_Wheel\_Hub\_Inside).
2.  Using 4 M2 screws from the Dynamixel MX-12W motor kits, fasten the
    hub (Kaya\_Wheel\_Hub\_Inside) to the horn of the Dynamixel. Tighten
    evenly. Be careful not to overtighten.
3.  Repeat for each motor.

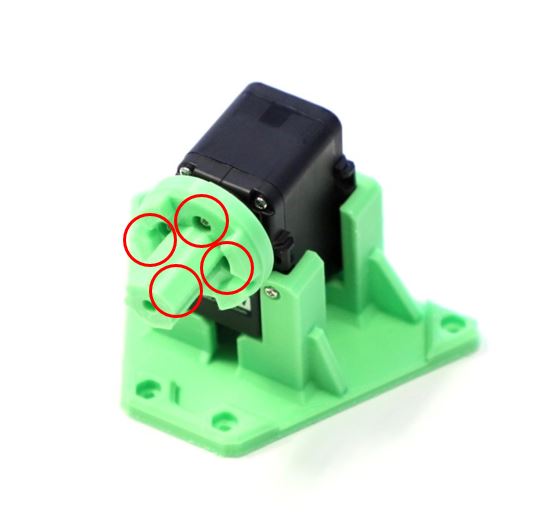
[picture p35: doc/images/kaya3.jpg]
    

**4 Cut and Crimp Power Wiring**

1.  Cut 9 sections of 18 AWG (4 black, 5 red) wire to length and strip
    insulation from the ends (3-5mm).
2.  Attach connectors according to the table using a suitable crimping
    tool. Take care to ensure that all connectors are mechanically
    secure and make good electrical contact.

    Refer to the following image, table and the Wiring Diagram when
    cutting and crimping wiring.

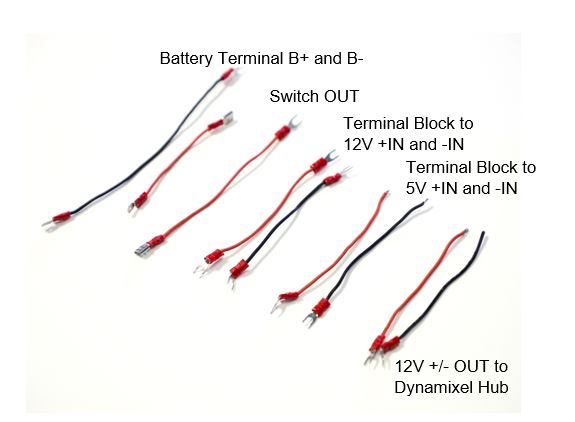
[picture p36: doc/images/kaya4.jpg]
    

<table style="width:100%;">
<colgroup>
<col width="14%" />
<col width="14%" />
<col width="14%" />
<col width="14%" />
<col width="14%" />
<col width="14%" />
<col width="14%" />
</colgroup>
<tbody>
<tr class="odd">
<td><strong>Wire#</strong></td>
<td><strong>Color</strong></td>
<td><strong>Length</strong></td>
<td><strong>Terminal 1 Connector</strong></td>
<td><strong>Terminal 1 Connection</strong></td>
<td><strong>Terminal 2 Connector</strong></td>
<td><strong>Terminal 2 Connection</strong></td>
</tr>
<tr class="even">
<td>1</td>
<td>Black</td>
<td>140 mm</td>
<td>Male Spade</td>
<td>Battery B-</td>
<td>Fork Spade</td>
<td>Terminal Block B-</td>
</tr>
<tr class="odd">
<td>2</td>
<td>Red</td>
<td>80 mm</td>
<td>Male Spade</td>
<td>Battery B+</td>
<td>Female Spade</td>
<td>Switch IN</td>
</tr>
<tr class="even">
<td>3</td>
<td>Red</td>
<td>140 mm</td>
<td>Female Spade</td>
<td>Switch OUT</td>
<td>Fork Spade</td>
<td>Terminal Block B+</td>
</tr>
<tr class="odd">
<td>4</td>
<td>Black</td>
<td>120 mm</td>
<td>Fork Spade</td>
<td>Terminal Block B-</td>
<td>Fork Spade</td>
<td>12V Regulator -IN</td>
</tr>
<tr class="even">
<td>5</td>
<td>Red</td>
<td>120 mm</td>
<td>Fork Spade</td>
<td>Terminal Block B+</td>
<td>Fork Spade</td>
<td>12V Regulator +IN</td>
</tr>
<tr class="odd">
<td>6</td>
<td>Black</td>
<td>120 mm</td>
<td>Fork Spade</td>
<td>Terminal Block B-</td>
<td>Bare Wire</td>
<td>5V Regulator -IN</td>
</tr>
<tr class="even">
<td>7</td>
<td>Red</td>
<td>120 mm</td>
<td>Fork Spade</td>
<td>Terminal Block B+</td>
<td>Bare Wire</td>
<td>5V Regulator +IN</td>
</tr>
<tr class="odd">
<td>8</td>
<td>Black</td>
<td>120 mm</td>
<td>Fork Spade</td>
<td>12V Regulator -OUT</td>
<td>Bare Wire</td>
<td>Dynamixel Hub -IN</td>
</tr>
<tr class="even">
<td>9</td>
<td>Red</td>
<td>120 mm</td>
<td>Fork Spade</td>
<td>12V Regulator +OUT</td>
<td>Bare Wire</td>
<td>Dynamixel Hub +IN</td>
</tr>
</tbody>
</table>

**5 Connect Battery Terminals to the Battery Holder**

1.  Place Battery terminal cables (wires \#1 and \#2) into slots in the
    battery holder (Kaya\_Battery\_Holder), paddles facing each other as
    depicted below. The B+ (red wire) should be seated in the slot
    nearest to the notch cut out of the battery holder. Push firmly on
    the top of the crimps to seat properly in the channels.

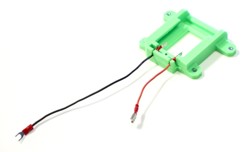
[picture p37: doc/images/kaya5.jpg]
    

2.  Secure the cables using the terminal holder
    (Kaya\_Battery\_Terminal\_Holder) and an M3 x 8mm screw. Check
    alignment with a battery, and use pliers to adjust the paddles until
    they align and seat properly. To avoid creating an electrical short
    between the battery terminals, cover any loose wire ends with
    electrical tape.

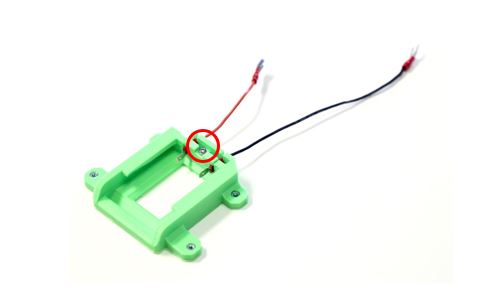
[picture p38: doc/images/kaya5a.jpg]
    

**6 Assemble the Frame**

1.  Attach each motor top plate (Kaya\_Motor\_Top\_Plate) to MakerBeams
    using 4 MakerBeam nuts and 4 M3 x 5mm screws at each corner. Slide
    MakerBeam nuts into channels first, 2 per side, and then align with
    the holes before fastening with screws.

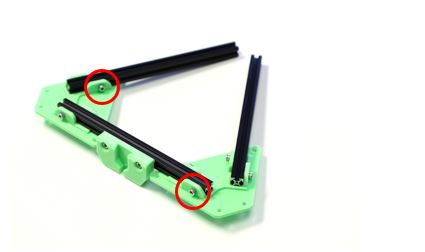
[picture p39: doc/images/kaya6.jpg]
    

2.  Between two motor top plates (Kaya\_Motor\_Top\_Plate), install
    Kaya\_Pusher\_Mount, remembering to slide nuts into place before
    attaching the second motor top plate.
3.  Assemble the full triangle and tighten all 12 screws evenly. The
    side with the pusher mount (Kaya\_Pusher\_Mount) is the front of
    Kaya, for the purposes of the rest of this procedure.

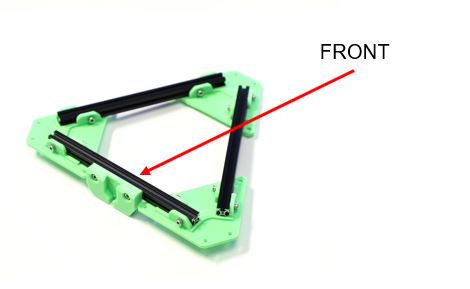
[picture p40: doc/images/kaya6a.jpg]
    

**7 Connect the Bottom Plate Assembly to the Motor Top Plate/MakerBeam
Frame**

1.  Attach each motor bottom plate (Kaya\_Motor\_Bottom\_Plate)
    assemblies to the frame in the correct configuration. The motor
    assembly tagged with Dynamixel ID 2 should sit opposite to the
    pusher mount (Kaya\_Pusher\_Mount), with the other two motor
    assemblies to the adjacent sides.
2.  Insert 4 M3 nuts into a motor bottom plate
    (Kaya\_Motor\_Bottom\_Plate), and attach to motor top plates
    (Kaya\_Motor\_Top\_Plate) with 4 M3 x 8mm screws. Repeat for each
    motor. Tighten all 12 screws evenly.

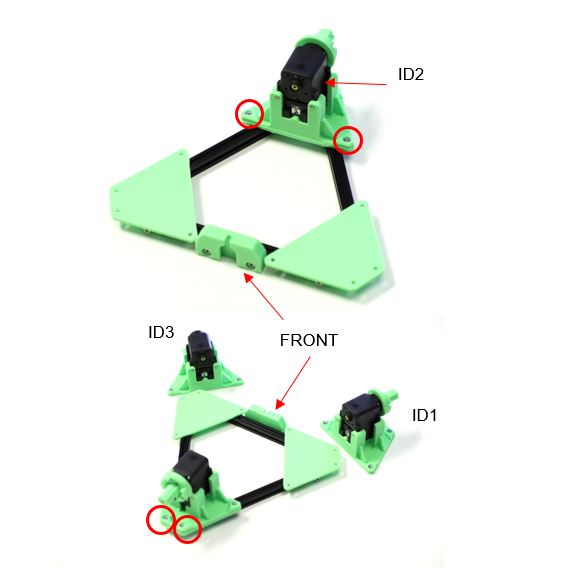
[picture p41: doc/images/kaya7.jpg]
    

**8 Connect Motor Wiring**

-   When all of the Dynamixel MX-12W servo motors have been assigned IDs
    (see step 1) and have been installed in the proper locations,
    connect them for power and data transmission using the cables from
    the Dynamixel MX-12W motor kits.

    All servo motors share common power and data lines, and communicate
    using data packets addressed by motor ID. For this reason, they may
    be connected in any order, or even wired individually to the
    Dynamixel Power Hub. For cable management purposes the best
    connection order is 1 - 3 - 2.

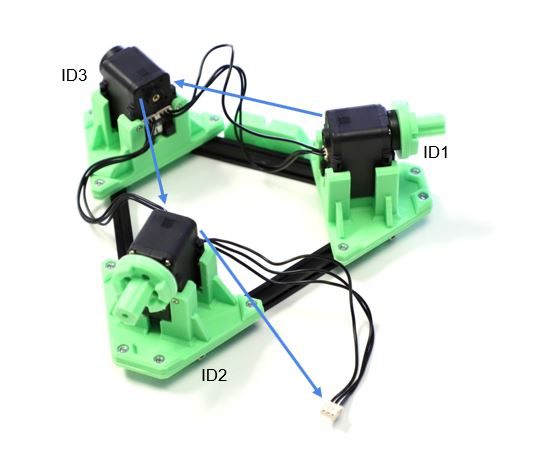
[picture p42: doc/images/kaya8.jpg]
    

**9 Mount the IMU**

1.  Solder male header pins to the IMU board. Arrange them with long
    ends on the labelled side of the board. Pins for 3V3, GND, SCL, and
    SDA will be used for I2C communication.
2.  Mount the IMU board with header pins facing towards the center of
    the electronics bay (Kaya\_Electronics\_Bay) using 2 M2 x 6mm
    screws, as shown.

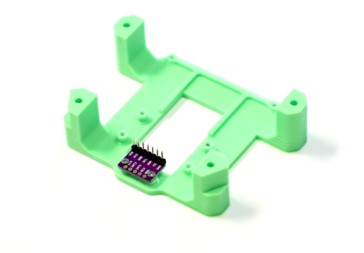
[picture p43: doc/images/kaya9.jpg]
> 

**10 Mount DC Regulators**

1.  Solder the blue screw terminals to the Pololu 5V 6A DC-DC Step-Down
    Regulator.
2.  Fasten the 5V regulator and 12V regulator to the electronics bay
    (Kaya\_Electronics\_Bay) with 6 M2 x 6mm screws. Ensure the
    orientation of these regulators matches the image, with IN+/- on the
    5V regulator on the same side as IN+/- on the 12V regulator.

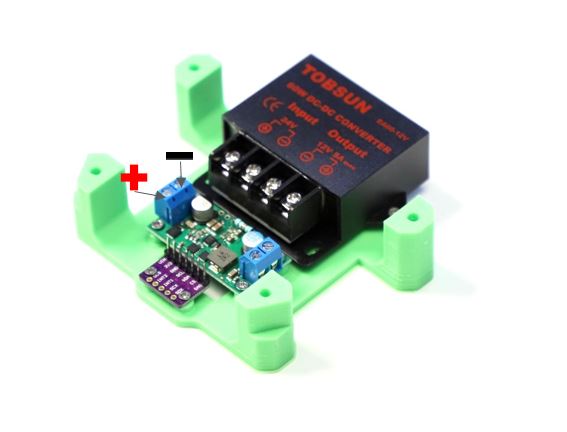
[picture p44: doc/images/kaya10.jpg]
    

**11 Connect IMU Wiring**

1.  Attach female-to-female electrical jumper wires to IMU leads (3V3,
    GND, SCL, and SDA). Make note of what color wires are attached to
    each pin, these will later be connected to the Jetson Nano GPIO
    pins.
2.  Optionally, use a dab of hot glue on the middle side of the headers
    to hold to the IMU pin headers firmly in place.

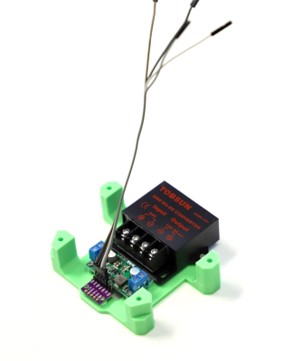
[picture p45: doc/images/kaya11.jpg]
    

See [Wire the BMI160 IMU to the Jetson Nano or Xavier](wire_bmi160_imu.md) for more information.

**12 Install Wi-Fi Antennas**

1.  Connect the antenna cables to the Wi-Fi antennas using the SMA screw
    terminal.
2.  Bend antennas to 90 degrees, and fit them in the designated channels
    on either side of the base (Kaya\_Nano\_Base).
3.  Fasten antennas in place using zip-ties, as shown.

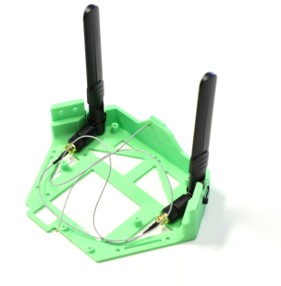
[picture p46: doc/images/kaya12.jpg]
    

**13 Attach the Jetson Nano Base to the Frame**

1.  Orient the Jetson Nano Base (Kaya\_Nano\_Base) so that the NVIDIA
    logo faces the Kaya pusher mount (Kaya\_Pusher\_Mount).
2.  Slide 1 MakerBeam nut onto the top of the front MakerBeam, and 2
    onto the other two MakerBeams. Fasten the front screw first, then
    position the other 4 down to side beams. Tighten all screws evenly.

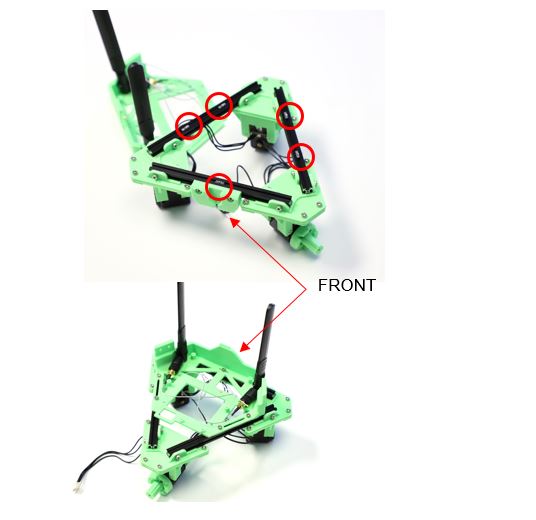
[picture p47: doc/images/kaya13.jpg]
    

**14 Connect the Battery Chassis Assembly to the New Frame Assembly**

1.  Stack the electronics bay (Kaya\_Electronics\_Bay) on top of the
    battery holder (Kaya\_Battery\_Holder) with the flat faces together,
    DC regulators face-up.
2.  Bring the top of the electronics bay (Kaya\_Electronics\_Bay) into
    contact with the bottom of the base (Kaya\_Nano\_Base), so that it
    sits in the center of the frame assembly, between the motors.
3.  Ensure that no cables are being pinched. Check that the front
    dynamixel cables are not on top of the 12V power supply. Then attach
    using 4 M3 x 35mm screws down through the base (Kaya\_Nano\_Base)
    and into 4 M3 nuts in the battery holder (Kaya\_Battery\_Holder).

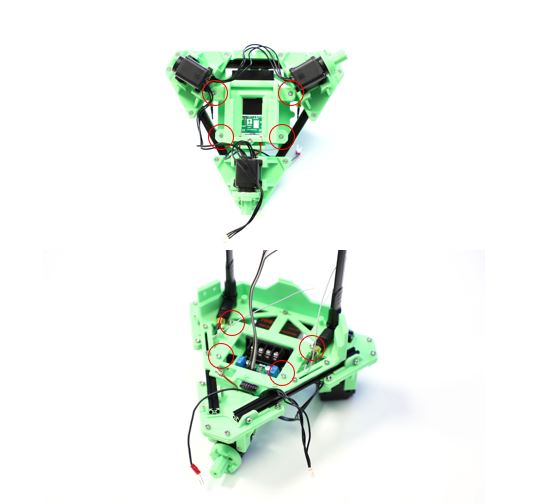
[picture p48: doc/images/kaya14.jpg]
    

**15 Prepare the Terminal Block**

-   Using terminal block jumpers, join the two leftmost terminal block
    connections together, then the two rightmost connections. This
    allows battery B+ and B- to be routed to the 12V and 5V DC
    regulators.

    Reference the Wiring Diagram when making electrical connections as
    outlined in the following steps.

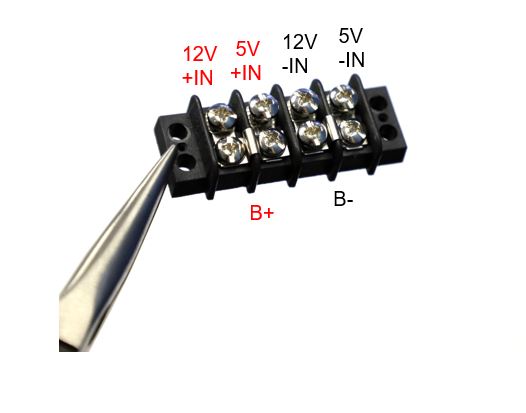
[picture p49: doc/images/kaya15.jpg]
    

**16 Install the Power Switch**

1.  Locate the B+ wire (\#2, Red) from the battery holder, and feed it
    through the switch hole at the rear of of the base
    (Kaya\_Nano\_Base). Connect the female spade connector to the middle
    switch terminal.
2.  Attach a second wire (\#3, Red, female spade to fork spade) to the
    outer switch terminal.
3.  Orient the switch so that the two terminals are closest to the
    inside of Kaya. Slightly bend the connected terminal wires to face
    the outside of Kaya as in the image. This helps them to clear the
    battery holder (Kaya\_Battery\_Holder) once installed.
4.  Feed the unattached fork spade connector through the switch hole and
    toward the rear of Kaya.
5.  Being careful to avoid pinched wires, snap the switch down into
    place.

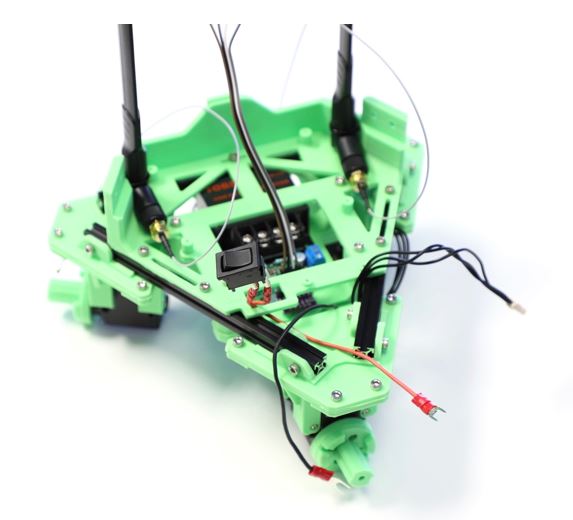
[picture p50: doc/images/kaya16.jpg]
    

**17 Connect Regulator Inputs**

1.  Pull the B- wire (\#1, Black) from the battery and the B+ wire from
    the switch (\#3, Red) to the rear of Kaya. Connect the fork spade
    connectors of these wires to the terminal block, referencing the
    Wiring Diagram. These wires should route neatly between the
    MakerBeams below the terminal block.

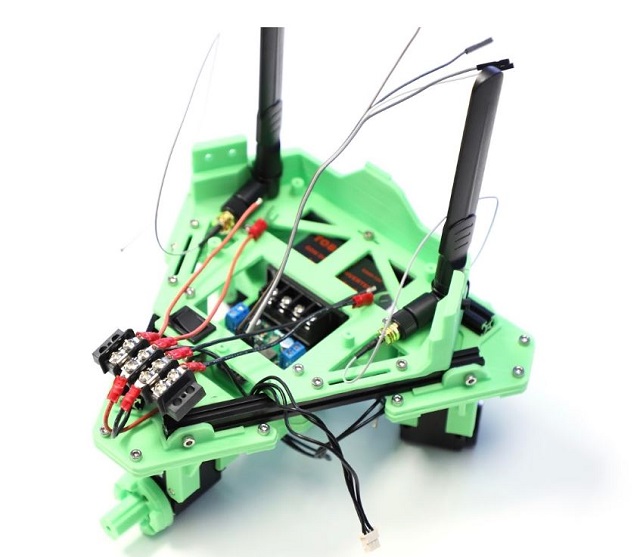
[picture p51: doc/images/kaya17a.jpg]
    

2.  Connect wires \#4 through \#7 to the terminal block using fork spade
    connectors. Reference photos and the Wiring Diagram for cable
    order. Bend the forks downward after they are connected onto the
    terminal block for a better fit.

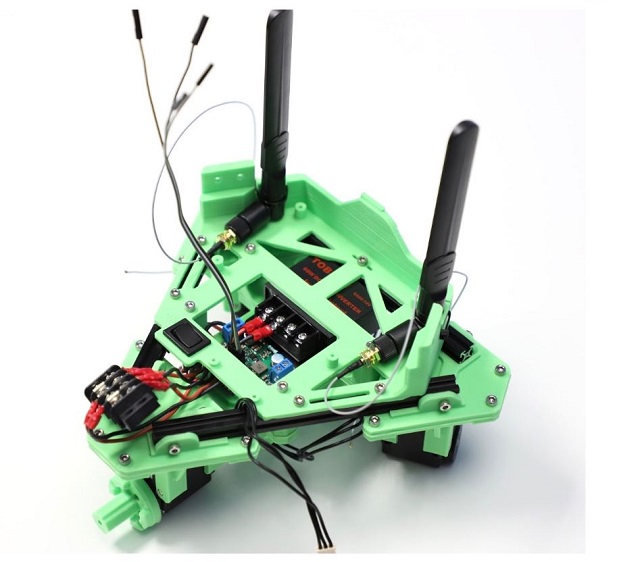
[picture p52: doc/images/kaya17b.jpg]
    

3.  Tuck the other cables underneath the base (Kaya\_Nano\_Base) and
    into the electronics bay (Kaya\_Electronics\_Bay). Connect cables
    \#4 and \#5 to the 12V regulator IN+/-, and cables \#6 and \#7 to
    the 5V regulator IN+/-. Note that the connections on the 12V
    regulator are ordered +IN, -IN, -OUT, +OUT, as indicated in the
    Wiring Diagram.

**18 Connect Regulator Outputs**

1.  Attach a 2.1 x 5.5mm male barrel plug pigtail to the 5V regulator
    out screw terminals. Note that the Brown wire is +, and the Blue
    wire is -. (Center positive polarity.)
2.  Connect the fork spade connectors of cables \#8 and \#9 to the 12V
    regulator OUT- and OUT+. Connect bare wire ends to the Dynamixel
    Power Hub screw terminals, routing the cables either back through or
    around the base (Kaya\_Nano\_Base).

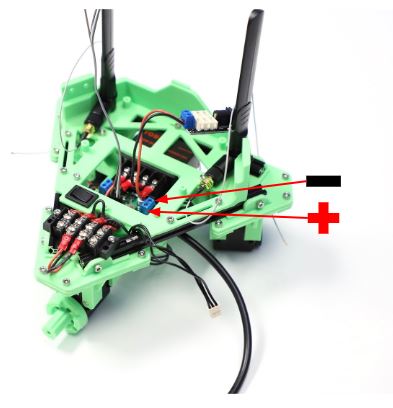
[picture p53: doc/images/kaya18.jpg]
    

**19 Mount the Terminal Block**

1.  Mount the terminal block to the frame with 3 MakerBeam nuts and 2 M3
    x 8mm screws. Slide one extra nut ahead of right side of terminal
    block for later use with the terminal block cover
    (Kaya\_Terminal\_Block\_Cover).
2.  Position the Terminal Block as far back as possible by using only
    the front set of mounting holes.

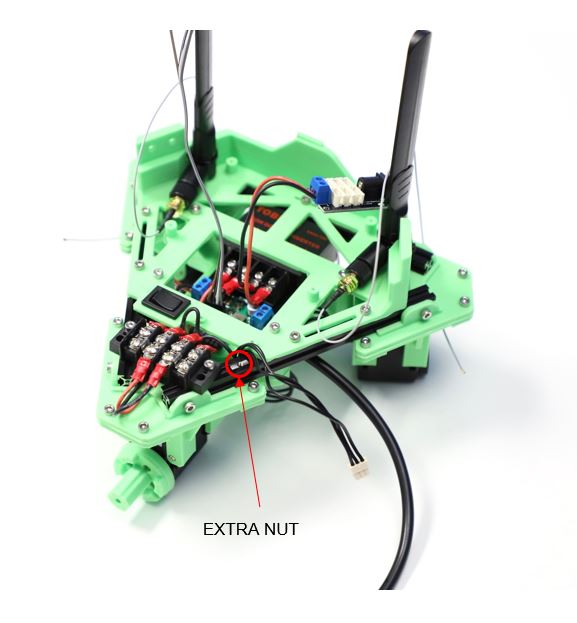
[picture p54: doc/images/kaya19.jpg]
    

**20 Mount the Dynamixel Power Hub**

1.  Connect the loose Dynamixel cable from servo motor ID3 to any port
    on the Dynamixel Power Hub.
2.  Use another Dynamixel cable to connect the USB2AX to the Dynamixel
    Power Hub. Mount the Dynamixel Power Hub to the base
    (Kaya\_Nano\_Base) with 2 M2x6 screws, as shown below.

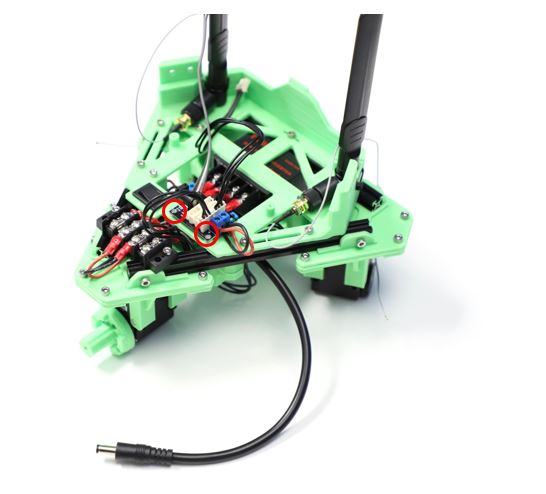
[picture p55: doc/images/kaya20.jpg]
    

**21 Connect the Wi-Fi Card**

-   Connect the small antenna cable connectors (U.FL / AMC / UMCC / IPX)
    to the Wi-Fi card. These should snap into place with vertical
    pressure, but can be difficult to work with. It may be helpful to
    lay the card on a flat surface for best leverage. Take care not to
    damage the connectors on the card, and avoid disconnecting and
    reconnecting if possible.

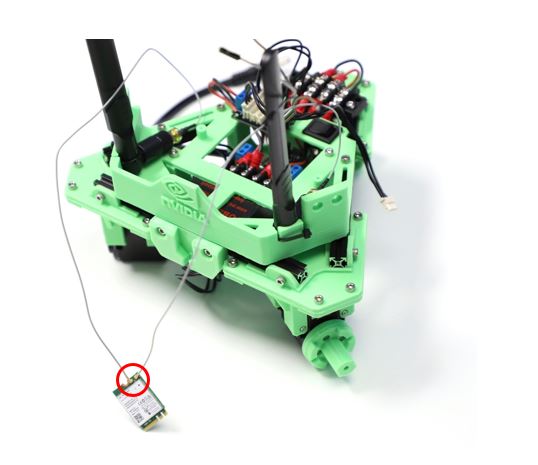
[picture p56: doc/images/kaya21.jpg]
    > 

**22 Install the Wi-Fi Card**

1.  Remove the Jetson Nano module from the carrier board by first
    removing 2 Phillips screws, then the 2 side latches.
2.  Connect the Wi-Fi card and secure with the included screw.

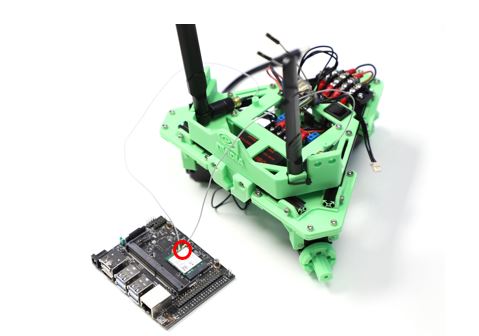
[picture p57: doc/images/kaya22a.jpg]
> 

1.  Reattach and secure the Jetson Nano module the carrier board.

**23 Mount the Jetson Nano**

1.  Mount the Jetson Nano Developer Kit to Kaya\_Nano\_Base using 4 M2 x
    6mm screws, as shown in the image below. For cable management, it
    may be helpful to coil the antenna cables beneath the Jetson Nano.
2.  Add a jumper across the header pins labeled “ADD JMPR TO DISABLE USB
    PWR” on the carrier board to allow the Jetson Nano to be powered via
    the 5V barrel jack connection.

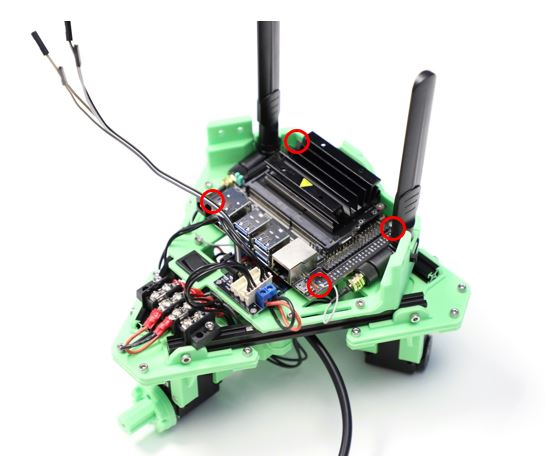
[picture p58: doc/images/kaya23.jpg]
> 

**24 Mount RealSense Camera**

1.  Attach the RealSense camera to Kaya\_Realsense\_Mount with 2 M3 x
    5mm screws.
2.  Use 3 M3 x 8mm screws and 3 M3 nuts to attach the camera mount
    (Kaya\_Realsense\_Mount) to the camera bridge
    (Kaya\_Realsense\_Bridge).
3.  Connect the USB-C cable to the RealSense camera.

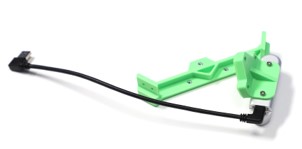
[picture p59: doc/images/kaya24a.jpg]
    

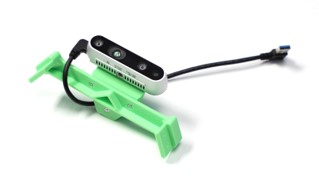
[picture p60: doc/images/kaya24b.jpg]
    

**25 Attach the RealSense Bridge to the Jetson Nano Base**

-   Use 4 M3 x 8mm and 4 M3 nuts to attach the camera bridge
    (Kaya\_Realsense\_Bridge) to the base (Kaya\_Nano\_Base).

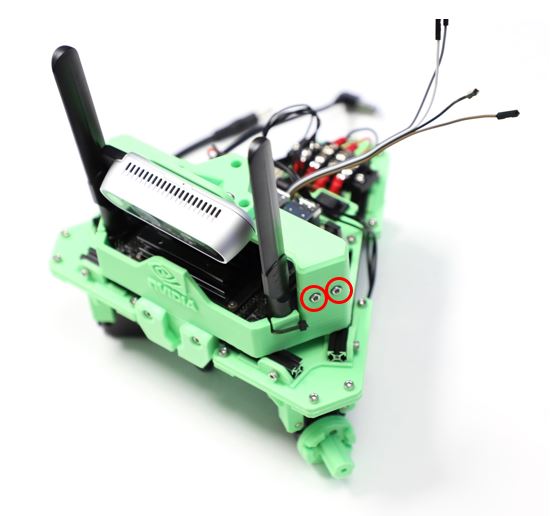
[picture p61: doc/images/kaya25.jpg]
    > 

**26 Mount the Wheels**

-   Attach each Omniwheel using 1 M3 x 35mm screw through the outside
    wheel hub (Kaya\_Wheel\_Hub\_Outside), the wheel itself, and then
    into the inside hub (Kaya\_Wheel\_Hub\_Inside). Take care not to
    overtighten.

    Threadlocker may be used to prevent loosening of these fasteners.

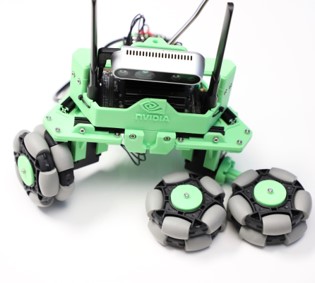
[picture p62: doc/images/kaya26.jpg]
    > 

**27 Attach the Terminal Block Cover**

-   Using the extra MakerBeam nut from step 19, attach the terminal
    block cover (Kaya\_Terminal\_Block\_Cover) using a M3 x 5mm screw.

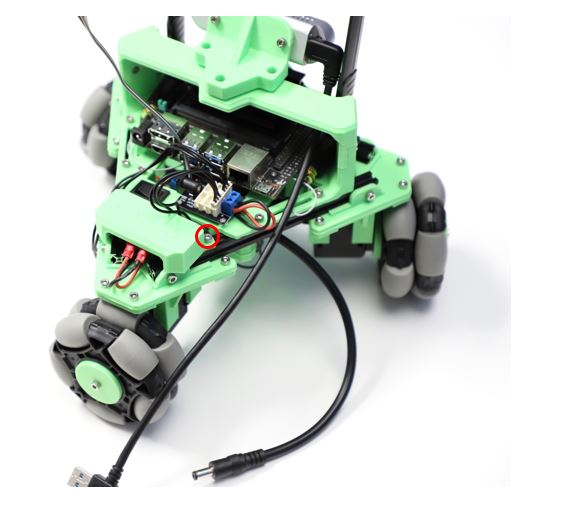
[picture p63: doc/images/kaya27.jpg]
    > 

**28 Connect Cables to Jetson Nano**

1.  Connect the RealSense camera and USB2AX to the top 2 USB connectors
    on the Nano.
2.  Ensure the power switch is **not** set to “ON”.
3.  Route the barrel plug cable from the 5V regulator behind the
    terminal block cover (Kaya\_Terminal\_Block\_Cover) and plug into
    the barrel jack input of Jetson Nano.

    **Never connect the 5V barrel plug cable to the barrel jack input of
    the Dynamixel Power Hub.** This may cause irreversible damage to the
    voltage regulators.

4.  Connect the jumper wires from the IMU to the Jetson Nano GPIO pins,
    referencing the Wiring Diagram and your earlier notes on wire
    colors.

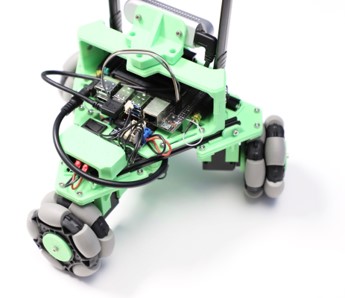
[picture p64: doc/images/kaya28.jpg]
    

**29 Clean Up Cables and Power On**

1.  Tuck the front Dynamixel cables up in front of 12V regulator and
    MakerBeam.
2.  Zip-tie other Dynamixel and power supply cables as desired.
3.  Install Battery and ensure it snaps into place. If there is
    resistance, check for cables and any remaining 3D printed support
    material, then ensure your terminals are not bent.
4.  Install the pusher (Kaya\_Pusher) by sliding it down into the pusher
    mount (Kaya\_Pusher\_Mount).

    Congratulations, you have fully assembled a Kaya robot! Have fun
    tinkering with your new creation and the Isaac Robot Engine!

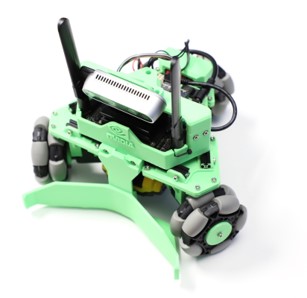
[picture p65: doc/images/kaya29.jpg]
    

Notes on Power-Hungry Applications
----------------------------------

You may encounter issues when running more demanding applications on
Jetson Nano, especially when running in “MAX-N” mode.

Be careful that 3D printed PLA plastic parts do not come into contact
with the heatsink if there are concerns with Jetson Nano overheating.
Kaya is not equipped with a fan to aid with cooling. The Jetson Nano
Developer Kit provides a 4-pin connector to accommodate 5V PWM fans.
However, adding a fan to Kaya requires removal or custom modification of
several 3D printed parts.

Raising the nominal output voltage of the 5V regulator can help
safeguard against the effects of transient voltage dips. This can be
accomplished by soldering a thru-hole resistor between the FB and GND
pins on the Pololu 5V regulator board. A resistor value of 82.5 kOhm
increases the nominal output voltage to 5.143V.

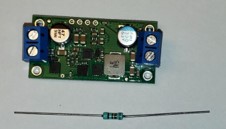
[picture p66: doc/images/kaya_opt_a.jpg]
> 

The following image shows the resistor correctly installed.

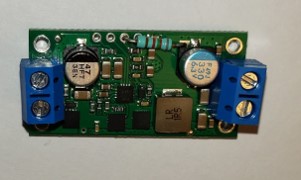
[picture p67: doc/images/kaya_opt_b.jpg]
> 

A capacitor (100-1000 uF) may also be placed across the regulator output
terminals to further safeguard against transient voltage fluctuations.
For more information, please reference the datasheet for the Microchip
MIC2101.

Running Isaac SDK on Kaya
-------------------------

Once you have assembled your Kaya, use the procedures in
[How to Get Started with Jetson Nano](nano.md) get started with Isaac on the Jetson Nano, and deploy
and run a couple of sample applications.

The Joystick Application
------------------------

The following steps deploy a simple joystick application that can be
used to control the Kaya robot.

1.  On the desktop system where the Isaac SDK is installed, enter the
    following command:

        ./engine/build/deploy.sh -d jetpack42 -h <nano_ip> -p //apps/kaya:joystick-pkg

2.  Change to the directory on your Nano and run the application with
    the following commands:

        cd deploy/<your_username>/joystick-pkg/
        ./apps/kaya/joystick

The Follow Me Application
-------------------------

The following steps deploy an application to have the Kaya robot
autonomously move towards a designated AprilTag fiducial. This
application combines AprilTag detection, path planning, control, and the
Kaya driver. It requires a working RealSense camera for AprilTag
detection and path planning, and a joystick to enable autonomous mode.

1.  On the desktop system where the Isaac SDK is installed, enter the
    following command:

        ./engine/build/deploy.sh -d jetpack42 -h <nano_ip> -p //apps/kaya:follow_me-pkg

    Where &lt;nano\_ip&gt; is the IP address of the Jetson Nano on the
    robot.

2.  Change to the directory on your Nano and run the application with
    the following commands:

        cd deploy/<your_username>/follow_me-pkg/
        ./apps/kaya/follow_me

3.  Open Isaac Sight on the desktop browser at &lt;nano\_ip&gt;:3000. In
    the Application Configuration panel on the right, click on
    fiducial\_as\_goal, and change the target\_fiducial\_id (default is
    "tag36h11\_9") to the id of the AprilTag in use.

    If you put the AprilTag within the RealSense camera's field of view,
    you should see in the Follower Kaya - Camera window that the april
    tag is detected, and a planned path shown in a blue line from the
    Kaya robot to the april tag.

4.  If you hold down the R1 button on the joystick, the Kaya robot
    enters autonomous mode, and moves towards the april tag. Move the
    april tag around while keeping it within the camera's view, and Kaya
    follows it around.

The Object Detection Application
--------------------------------

This application uses YOLO (tiny-yolov3) on Kaya to perform object
detection. The YOLO model is trained to recognize a few common objects
in these three classes for trash classification: compost (apple,
banana), metal (soda can), paper (paper box and small cardboard box).
Here are the steps for running this application.

1.  On the desktop system where the Isaac SDK is installed, enter the
    following command:

        ./engine/build/deploy.sh -d jetpack42 -h <nano_ip> -p //apps/kaya:object_detection-pkg

2.  Change to the directory on your Nano and run the application with
    the following commands:

        cd deploy/<your_username>/object_detection-pkg/
        ./apps/kaya/object_detection_kaya

    Open Isaac Sight on the desktop browser at &lt;nano\_ip&gt;:3000.
    You should be able to see the live camera image.

3.  Place an apple or a soda can in front of Kaya's camera, and you
    should see a bounding box around the object labeled as compost or
    metal, respectively.

The Mapping Application
-----------------------

The gmapping application demonstrates use of the Kaya robot to build an
occupancy map of its environment. Kaya uses the Intel RealSense camera
to perceive depth of obstacles, and wheel odometry and IMU to update its
own state. Obstacle depth and robot state information are published to
the host to build up a map.

This application has two parts: gmapping\_distributed\_kaya that runs on
the Kaya robot, and gmapping\_distributed\_host that runs on the host
machine.

1.  On the desktop system where the Isaac SDK is installed, enter the
    following command:

        ./engine/build/deploy.sh -d jetpack42 -h <nano_ip> -p //apps/kaya:gmapping_distributed_kaya-pkg

2.  Change to the directory on your Nano and run the application with
    the following commands:

        cd deploy/<your_username>/gmapping_distributed_kaya-pkg/
        ./apps/kaya/gmapping_distributed_kaya

    Open Isaac Sight on the desktop browser at &lt;nano\_ip&gt;:3000.
    You should be able to see the camera RGB and depth image, as well as
    plot of the robot state.

3.  Use the joystick to drive Kaya around and you should see the robot
    state being updated.
4.  On the desktop system, open
    app/kaya/gmapping\_distributed\_host.app.json and change the
    tcp-subscriber host from "YOUR\_NANO\_IP\_HERE" to the IP address of
    the Jetson Nano on the robot (&lt;nano\_ip&gt;).
5.  Build and run the host application with the following commands:

        bazel build //apps/kaya:gmapping_distributed_host
        bazel run //apps/kaya:gmapping_distributed_host

6.  Open Isaac Sight on the desktop at localhost:3000. You should be
    able to see the map Kaya is building. Use the joystick to drive Kaya
    around and observe the map updates.

    If you see performance issues with the map update, go to the Kaya
    page of Isaac Sight webpage and disable camera RGB and depth
    visualization (uncheck Channels - viewer).

IMU and Motor Permissions
-------------------------

Kaya uses an IMU that connects using I2C protocol and motors that are
connected through USB. Therefore the following commands need to be
executed on Nano once. Please start a new terminal after running these
commands.

    sudo adduser $USER dialout
    sudo adduser $USER i2c

For more information on the IMU, see the [Wire the BMI160 IMU to the Jetson Nano or Xavier](wire_bmi160_imu.md) section of this
document.

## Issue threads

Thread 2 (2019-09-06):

Step 26 screw is too small for wheel

EricRohlfs, 2019-09-06:
FYI, I am posting this on behalf of another person.

On step 26, something is not correct.  The screw is too small for the printed part.
Does:
- the screw need to be bigger (maybe M4 x35mm)?
-  Or the cad files need adjusting?
- Or am I just doing it wrong?

The instructions are quoted below.
> 26 Mount the Wheels
>
> Attach each Omniwheel using 1 M3 x 35mm screw through the outside wheel hub ...

Files that may need adjusting.
https://github.com/nvidia-isaac/kaya-robot/blob/master/cad-files/Kaya_Wheel_Hub_Outside.stl

https://github.com/nvidia-isaac/kaya-robot/blob/master/cad-files/Kaya_Wheel_Hub_Inside.stl

kenvidia, 2019-09-06:
Hi Eric,

The screws which are used to attach the wheels do not thread into the plastic. Instead, they thread into the "[M3 18mm threaded standoff](https://www.mcmaster.com/95947a525)" which fits into the hexagonal hole on the backside of Kaya_Wheel_Hub_Inside.

Does this help clarify the assembly step?

Closed 2020-05-29.

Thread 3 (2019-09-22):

Dynamixel setting IDs - not recognizing that motor is connected

vnguyen13, 2019-09-22:
Can someone give me a diagram of how you connected the Dynamixel motors / power hub / U2D2 together to set the IDs for the motors? When I open the RoboPlus software's wizard, it doesn't show that it's connected.

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

kenvidia, 2019-09-26:
Hi vnguyen13,

Connection for setting the IDs is essentially the same as the final configuration, but you need to make sure that you only connect one motor at a time, as they all share the same ID before being configured. This tutorial does a pretty good job of walking you through the process in more detail than the Kaya assembly instructions:

https://learn.trossenrobotics.com/projects/194-setting-dynamixel-ax-and-mx-series-firmware-id-and-baud-with-roboplus-1-0.html

vnguyen13, 2019-09-26:
Thanks @kenvidia! It looks like the only thing I did out of order is I plugged in the motor and then started up the software. So i'll give it a try.

I did notice that once I plug in the motor and the U2D2 to the 6-port AX/MX Power hub, that the voltage across the power hub's power input supply reads 1.2V instead of 12V. I'm not sure if this is normal behavior. When I unplug the motor, the power reads 12V. I'm using the 24V li-ion battery going into the 24V-12V step down regulator as shown in the instructions.

kenvidia, 2019-09-26:
Hi @vnguyen13 , you shouldn't see a voltage drop when connecting the motors. You might see a brief dip when the motors were moving if you were measuring with an oscilloscope, but this shouldn't be noticeable at all with a multimeter.

Perhaps there is a wiring issue somewhere? Are you sure that the polarity is correct on the barrel connector for the power hub? (center positive, outside negative)

I don't think that the order of plugging in the motor should matter, as long as you manually scan for Dynamixel addresses.

vnguyen13, 2019-09-27:
Thanks @kenvidia . I checked the polarity, and it is correct. In the instructions it actually doesn't use the barrel connector to go to the power hub. It uses the bare wire ended wires that come out of the 24V-12V step-down regulator.

I have a 12V power supply coming in today so that I can use that to power the power hub instead of the bare wires. That can at least let me know if the step-down regulator is having issues. Thanks!

kenvidia, 2019-09-30:
Hi @vnguyen13 ,

Yes, I realized after making that post that I was mis-remembering the power connections for the hub. Please do not plug the 5V barrel jack for the Nano into the power hub, or it may damage the regulators. Hopefully you have better luck with the new 12V supply.

Closed 2020-05-29.

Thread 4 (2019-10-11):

The Mapping Application

bigboss10186, 2019-10-11:
First of all, thank you for your sharing. I have made kaya and hope to learn more from it. About The Mapping Application, I would like to know what The algorithm is and how to realize this function?
I didn't get the answer I wanted from
https://docs.nvidia.com/isaac/isaac/doc/tutorials/assemble_kaya.html#the-mapping-application

kenvidia, 2020-05-29:
Questions about Isaac SDK can be asked and answered on the NVIDIA Developer Forums:

https://forums.developer.nvidia.com/c/agx-autonomous-machines/isaac/sdk/68

Closed 2020-05-29.

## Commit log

2019-06-17 add content from Isaac SDK release 2019.1
    CAD files from Kaya_Robot_Reference_Design_20190411.zip. Converted 2019.1 versions of assemble_kaya.rst, nano.rst, wire_bmi160_imu.rst.
    [Kaya_Battery_Holder.iges, Kaya_Battery_Holder.step, Kaya_Battery_Holder.stl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]
2019-06-19 update cad-files download link
